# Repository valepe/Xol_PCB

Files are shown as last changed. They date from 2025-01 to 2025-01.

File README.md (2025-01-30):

# Xol PCB

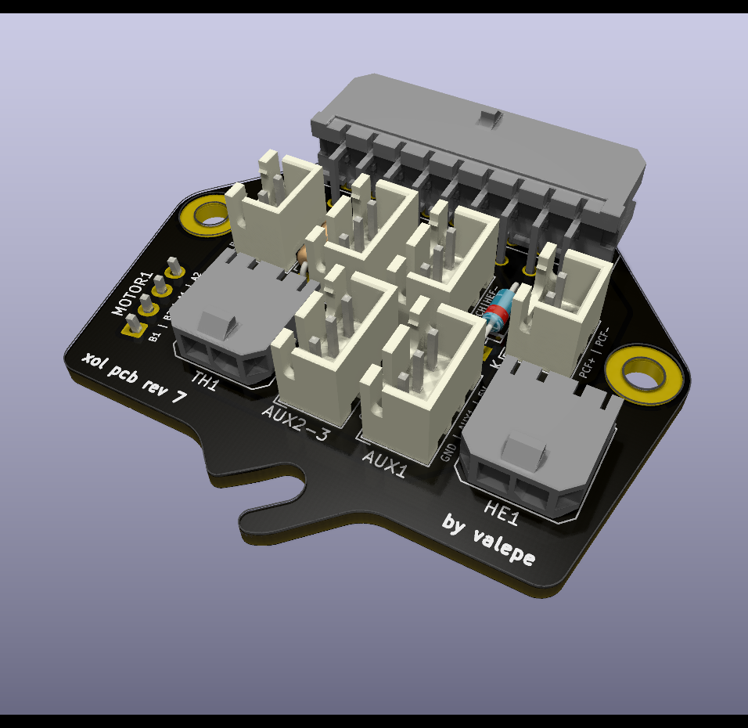
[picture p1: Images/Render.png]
Render

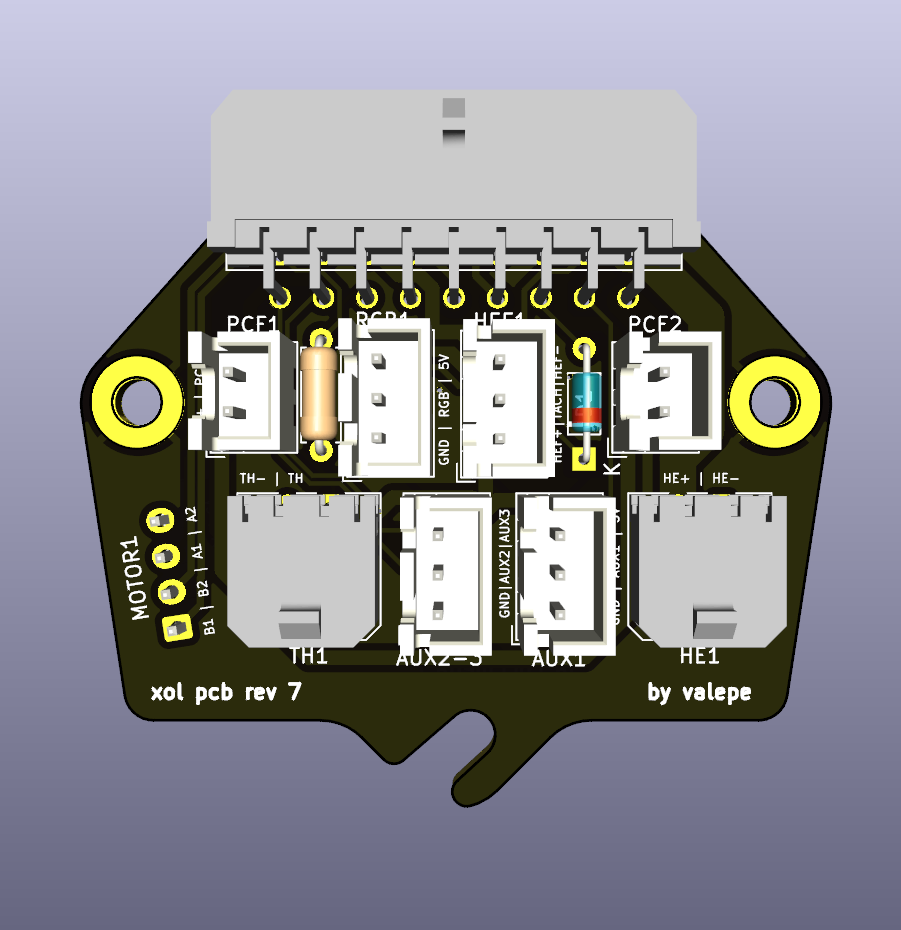
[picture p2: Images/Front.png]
Front

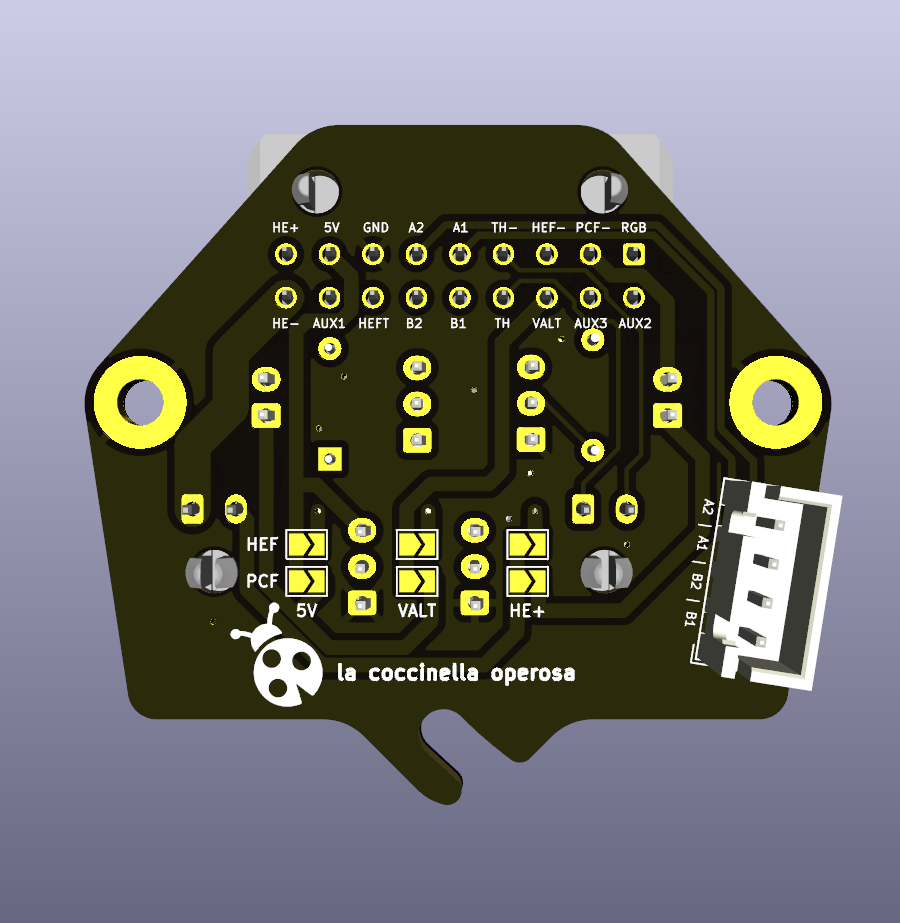
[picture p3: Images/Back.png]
Back


This is a PCB made for Armchair Engineering's [Xol Toolhead](https://github.com/Armchair-Engineering/Xol-Toolhead), featuring:
* One hotend cooling fan JST-XH connectors with diode for tach signal
* Two part cooling  fan JST-XH connectors
* One heater Micro-Fit connector
* One thermistor Micro-Fit connector
* One Neopixel JST-XH connector with resistor for the data line
* Two auxiliary JST-XH connectors
* One extruder motor connector
* Selectable fan voltage (5V, Alt, 24V)
* Integrated mount for carriage screw

I customized the Xol Toolhead board by [ruiqimao](https://github.com/ruiqimao/VoronStuff/tree/main/Xol_PCB) to suite my needs:
* A three pins connector for the hotend fan with tach signal and its diode
* A resistor for the RGB data line to avoid signal noise for the cable length
* Three AUX pins for X-endstop and the two filament sensors

**ATTENTION!** This pcb isn't pin compatible with ruiqimao one starting from the main connector (from 16 to 18 pins). Even the thermistor and hotend connectors are swapped. Check carefully the pinout!

## BOM

In addition to the PCB, the following things are needed:

| Part | Quantity | Link |
|:-:|:-:|:-:|
| Molex Micro-Fit 3.0 430451800 | 1 | [DigiKey](https://www.digikey.com/en/products/detail/molex/0430451800/531425) |
| Molex Micro-Fit 3.0 430650200 | 2 | [DigiKey](https://www.digikey.com/en/products/detail/molex/0436500200/268989) |
| JST B2B-XH-A | 2 | [DigiKey](https://www.digikey.com/en/products/detail/jst-sales-america-inc./B2B-XH-A(LF)(SN)/1651045) |
| JST B3B-XH-A | 4 | [DigiKey](https://www.digikey.com/en/products/detail/jst-sales-america-inc./B3B-XH-A/1651046) |
| JST B4B-XH-A | 1 | [DigiKey](https://www.digikey.com/en/products/detail/jst-sales-america-inc./B4B-XH-A(LF)(SN)/1651047) |
| BAT85 diode | 1 | [DigiKey](https://www.digikey.com/en/products/detail/nexperia-usa-inc/BAT85-133/1232135) |
| 470 Ohm resistor | 1 | [DigiKey](https://www.digikey.com/en/products/detail/stackpole-electronics-inc/CF14JT470R/1741440) |

## Pinout

From the point of view looking directly at the **wiring harness connector**:

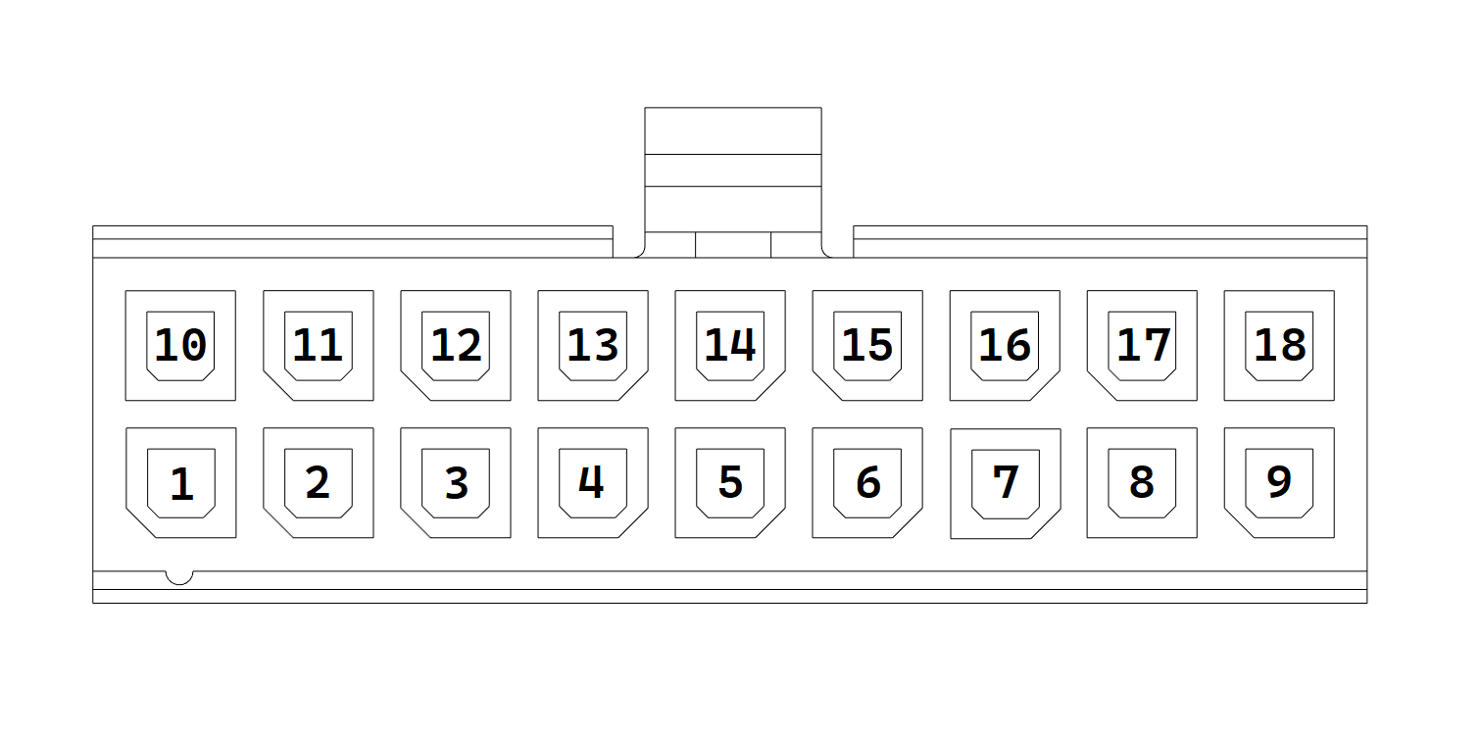
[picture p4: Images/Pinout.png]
Pinout


| Pin | Usage | Pin | Usage |
|:-:|:-:|:-:|:-:|
| 1 | Neopixel | 10 | Auxiliary 2 |
| 2 | Part cooling fan ground | 11 | Auxiliary 3 |
| 3 | Hotend fan ground | 12 | Alt voltage |
| 4 | Thermistor ground | 13 | Thermistor |
| 5 | Motor A1 | 14 | Motor B1 |
| 6 | Motor A2 | 15 | Motor B2 |
| 7 | Ground | 16 | Hotend fan tach |
| 8 | 5V | 17 | Auxiliary 1 |
| 9 | Hotend voltage | 18 | Hotend ground |

## Selectable fan voltage

There are two sets of solder jumpers, one for each type of fan, that should be bridged to select the fan voltage.

## Extruder compatibility
The PCB and strain relief are designed with only the [Sherpa Mini](https://github.com/Annex-Engineering/Sherpa_Mini-Extruder) in mind. **Usage with other extruders may require the motor connector to be swapped to the back side.**

## Credits

Credits to the great work of XOL Toolhead board by [ruiqimao](https://github.com/ruiqimao/VoronStuff/tree/main/Xol_PCB).

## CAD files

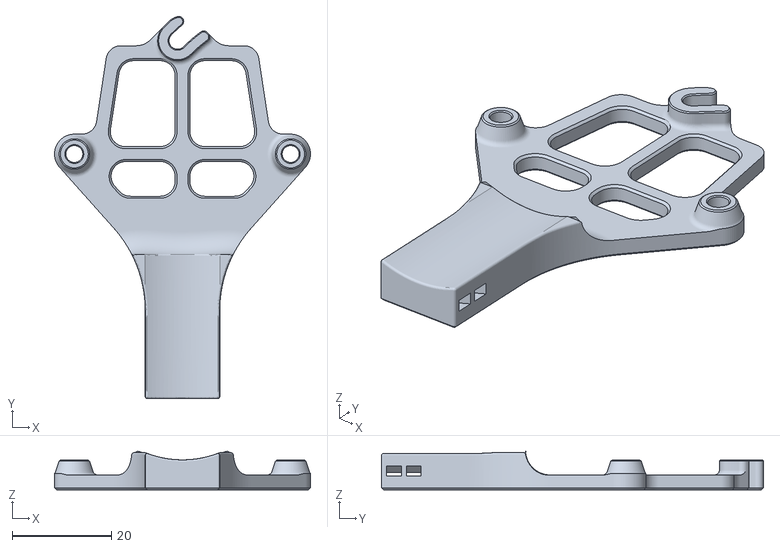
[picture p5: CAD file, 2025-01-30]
STLs/Strain_Relief_Sherpa_Mini.stl
51.5 x 76.9 x 7.79

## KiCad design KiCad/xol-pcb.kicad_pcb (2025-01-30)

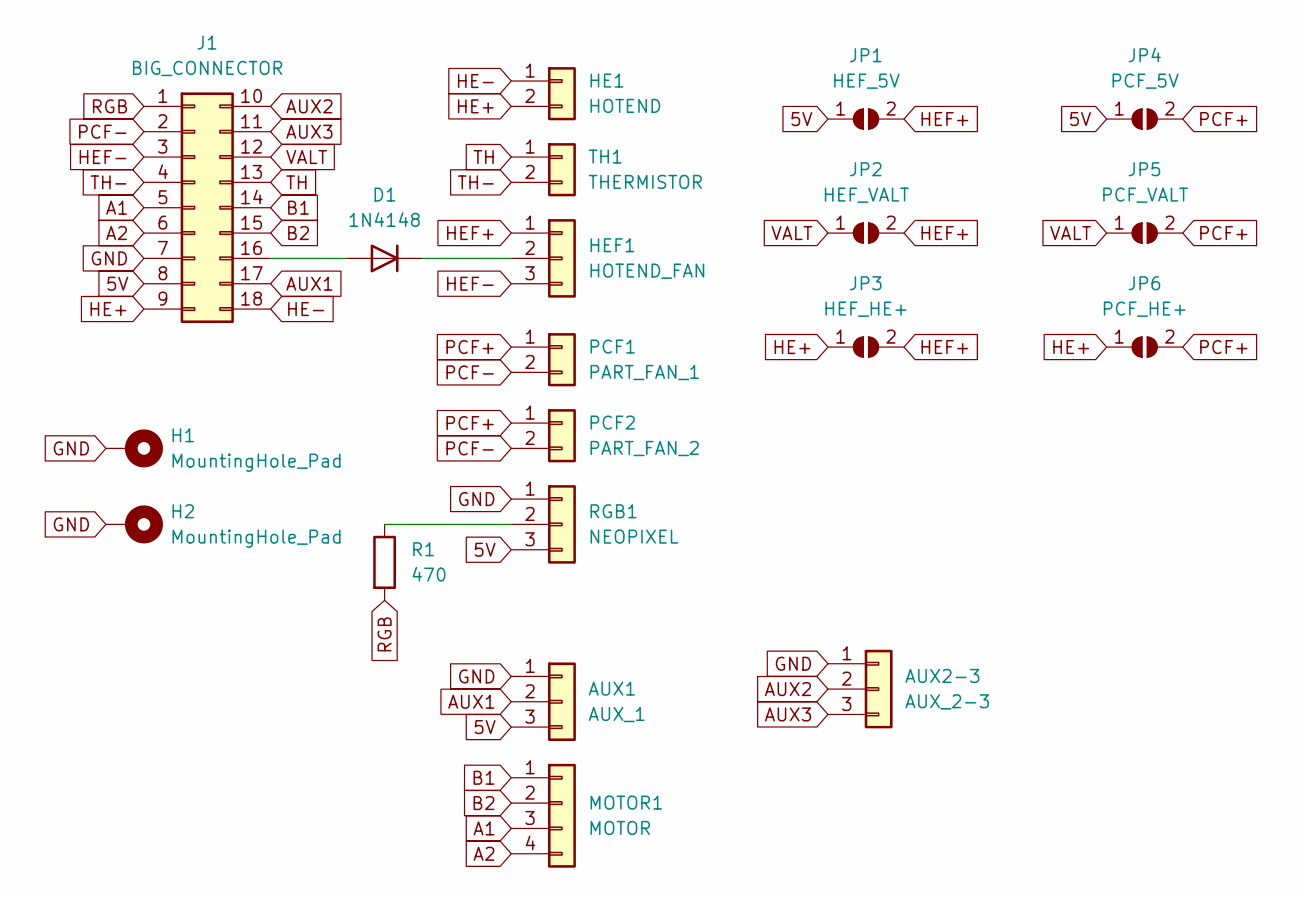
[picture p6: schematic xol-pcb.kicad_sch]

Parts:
AUX1: AUX_1; JST_XH_B3B-XH-A_1x03_P2.50mm_Vertical
AUX2-3: AUX_2-3; JST_XH_B3B-XH-A_1x03_P2.50mm_Vertical
D1: 1N4148; D_DO-35_SOD27_P7.62mm_Horizontal
H1, H2: MountingHole_Pad; MountingHole_3.2mm_M3_Pad
HE1: HOTEND; Molex_Micro-Fit_3.0_43650-0200_1x02_P3.00mm_Horizontal
HEF1: HOTEND_FAN; JST_XH_B3B-XH-A_1x03_P2.50mm_Vertical
J1: BIG_CONNECTOR; Molex_Micro-Fit_3.0_43045-1800_2x09_P3.00mm_Horizontal
JP1: HEF_5V; SolderJumper-2_P1.3mm_Open_TrianglePad1.0x1.5mm
JP2: HEF_VALT; SolderJumper-2_P1.3mm_Open_TrianglePad1.0x1.5mm
JP3: HEF_HE+; SolderJumper-2_P1.3mm_Open_TrianglePad1.0x1.5mm
JP4: PCF_5V; SolderJumper-2_P1.3mm_Open_TrianglePad1.0x1.5mm
JP5: PCF_VALT; SolderJumper-2_P1.3mm_Open_TrianglePad1.0x1.5mm
JP6: PCF_HE+; SolderJumper-2_P1.3mm_Open_TrianglePad1.0x1.5mm
MOTOR1: MOTOR; JST_XH_B4B-XH-A_1x04_P2.50mm_Vertical
PCF1: PART_FAN_1; JST_XH_B2B-XH-A_1x02_P2.50mm_Vertical
PCF2: PART_FAN_2; JST_XH_B2B-XH-A_1x02_P2.50mm_Vertical
R1: 470; R_Axial_DIN0207_L6.3mm_D2.5mm_P7.62mm_Horizontal
RGB1: NEOPIXEL; JST_XH_B3B-XH-A_1x03_P2.50mm_Vertical
TH1: THERMISTOR; Molex_Micro-Fit_3.0_43650-0200_1x02_P3.00mm_Horizontal

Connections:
5V: AUX1.3, J1.8, JP1.1 (A), JP4.1 (A), RGB1.3
A1: J1.5, MOTOR1.3
A2: J1.6, MOTOR1.4
AUX1: AUX1.2, J1.17
AUX2: AUX2-3.2, J1.10
AUX3: AUX2-3.3, J1.11
B1: J1.14, MOTOR1.1
B2: J1.15, MOTOR1.2
GND: AUX1.1, AUX2-3.1, H1.1, H2.1, J1.7, RGB1.1
HE+: HE1.2, J1.9, JP3.1 (A), JP6.1 (A)
HE-: HE1.1, J1.18
HEF+: HEF1.1, JP1.2 (B), JP2.2 (B), JP3.2 (B)
HEF-: HEF1.3, J1.3
unnamed: D1.2 (A), J1.16
unnamed: D1.1 (K), HEF1.2
unnamed: R1.1, RGB1.2
PCF+: JP4.2 (B), JP5.2 (B), JP6.2 (B), PCF1.1, PCF2.1
PCF-: J1.2, PCF1.2, PCF2.2
RGB: J1.1, R1.2
TH: J1.13, TH1.1
TH-: J1.4, TH1.2
VALT: J1.12, JP2.1 (A), JP5.1 (A)

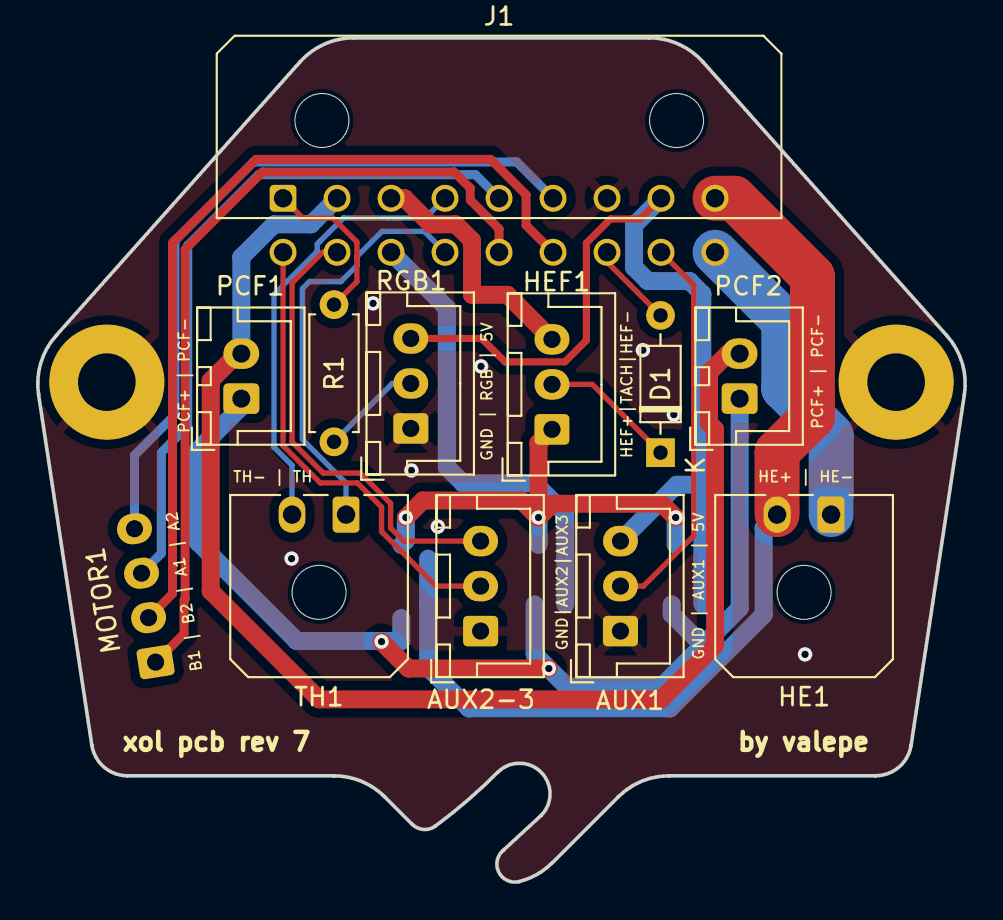
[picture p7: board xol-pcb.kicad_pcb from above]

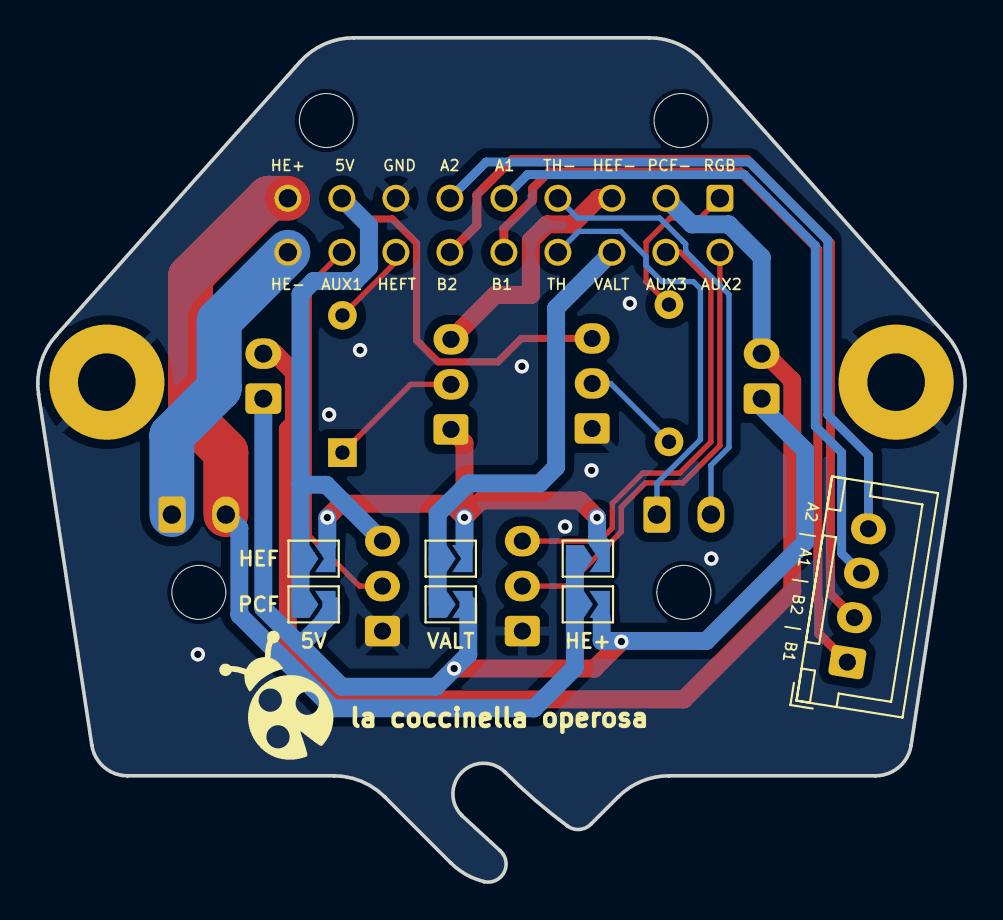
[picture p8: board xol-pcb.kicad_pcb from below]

Board: 2 copper layers, 51.5 x 46.9 mm, 20 parts (7 on the bottom side), 22 nets.
